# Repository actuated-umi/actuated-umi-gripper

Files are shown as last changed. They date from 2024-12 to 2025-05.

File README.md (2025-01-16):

# actuated-umi-gripper

<!-- PROJECT LOGO -->
<br />
<div align="center">
  <a href="https://github.com/actuated-umi/actuated-umi-gripper">
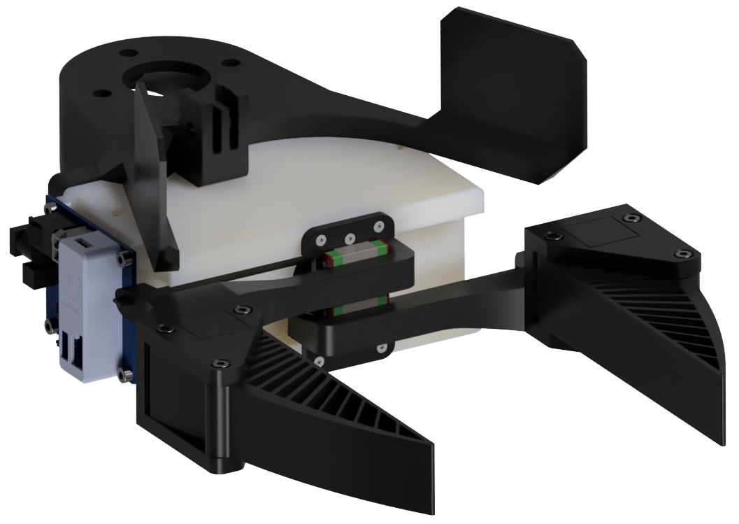
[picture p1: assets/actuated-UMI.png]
actuated-umi-gripper
    
  </a>

  <h3 align="center">Actuated UMI Gripper</h3>
  <h5 align="center">Erik Helmut*, Niklas Funk*, Tim Schneider, Jan Peters<br><em>*Equal contribution</em></h5>

  <p align="center">
    This repository provides an actuated, open-source version of the popular <a href="https://umi-gripper.github.io">UMI gripper</a>. 
    Designed to be cost-effective and modular, this gripper uses 3D-printed components to ensure accessibility and reproducibility. 
    With a Dynamixel motor for actuation, you can assemble the gripper yourself using the included design files and guidelines. 
    This repository contains the mechanical design files and printable components, enabling you to build and customize the gripper to suit your needs.
    This project would not have been possible without the earlier efforts of Chi et al. (2024) and the work of Clayton Haight. For more information about the prior works, please see the <a href="#acknowledgements">Acknowledgements</a> Section. <br />
    <a href="https://actuated-umi.github.io"><strong>For more information about actuated-UMI, visit the project page »</strong></a> <br />
  </p>
</div>

```
@inproceedings{helmut2024actuatedumi,
  author = {Helmut, Erik and Funk, Niklas and Schneider, Tim and Peters, Jan},
  title = {Actuated Version of the Universal Manipulation Interface Gripper},
  year = {2024},
  url  = {https://actuated-umi.github.io/}
}
```

<!-- TABLE OF CONTENTS -->
<details>
  <summary>Table of Contents</summary>
  <ol>
    <li>
      <a href="#bill-of-materials-bom">Bill of Materials (BoM)</a>
    </li>
    <li>
      <a href="#3d-printing-details">3D Printing Details</a>
    </li>
    <li>
      <a href="#assembly-guide">Assembly Guide</a>
    </li>
    <li>
      <a href="#usage">Usage</a>
    </li>
    <li>
      <a href="#acknowledgements">Acknowledgements</a>
    </li>
    <li>
      <a href="#license">License</a>
    </li>
    <li>
      <a href="#questions-and-contributing">Questions and Contributing</a>
    </li>
  </ol>
</details>

<!-- Bill of Materials -->
## Bill of Materials (BoM)
To build the actuated UMI gripper, you will need the following components. The list includes all necessary parts, along with links to purchase them online.

| Item | Quantity | Link |
|---|---|---|
| DYNAMIXEL XL430-W250-T | 1 | [MyBotShop](https://www.mybotshop.de/DYNAMIXEL-XL430-W250-T) |
| ROBOTIS DYNAMIXEL U2D2 | 1 | [MyBotShop](https://www.mybotshop.de/ROBOTIS-DYNAMIXEL-U2D2) |
| ROBOTIS DYNAMIXEL U2D2 POWER HUB | 1 | [MyBotShop](https://www.mybotshop.de/ROBOTIS-DYNAMIXEL-U2D2-Power-Hub) |
| Constant Force Spring (0.1x8x110) | 2 | [AliExpress](https://de.aliexpress.com/item/1005002310168061.html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) |
| Linear Rail & Carriage (80mm - MGN7C) | 2 | [AliExpress](https://de.aliexpress.com/item/1005004432783865.html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) |
| Flat Belt (width 5mm, thickness 1mm, length 300mm) | 1 | [KeilriemenExpress](https://www.keilriemenexpress.de/weitere-produkte/flachriemen-t150/neoprene-29306.html) |
| Heat Sets | 1 | [Amazon](https://www.amazon.de/Gewindeeinsatz-Einpressmutter-Gewindebuchsen-Kunststoff-Box-Kunststoffteiledurch/dp/B09B7F2XM3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) |
| Cylindrical Head Screws & Nuts (M3) | 1 | [Amazon](https://www.amazon.de/Sechskopf-Knopf-Zylinderschrauben-Gewindeschrauben-Sechskantschrauben-Maschinenschrauben/dp/B0B3MGZ7T2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ÅMÅŽÕÑ&crid=2AKHUVV2YXU0R&dib=eyJ2IjoiMSJ9.Gr0nOLkGHe8tC7VVlCThbb-3XEpHcX-eWT53-YGcYCqxmfHRqyxQLlBbVedU2xbw7nP-bcgj16am2vRgFkklYlSRtz3UCmgdAbns-Q1GhsDcldaA-3Puam8GKie6pPorMDHJwOL2cOysa3R_sP7CG7DVoxLh-96c7eJ_UxtuZCTM8XhOxgb_WTXR_o_CSQl1SargHb3wQWcaPaLm3-gPLkItAvxHlmyiryJryzrxORqWLVMNvA3O3HU5WPSbSJvE5MbQQ0Ben3iprgAdZbD7leyK8TchqTifKjEYljH00C23uNk1ystsyp9U24Gqirlc7gRdRJsspQR60bryparifMY5C1GV1TeXAIPXu3wbRVCFtpicU6AtxQ9DqY7fKWFWpiEUZiY6qYQhPYT9wVg1EHDFCk71AVnBrrAe34FDk-DPz8iuSDiNOT6HQFQlxaEw.pLT4ZCgQSOE5yQdMa6NFprSqQCqqWs3QW83IuaejpdI&dib_tag=se&keywords=m3x40&nsdOptOutParam=true&qid=1734961433&sprefix=m3x40%2Caps%2C150&sr=8-6&th=1) |
| Flat Head Screws (M2) | 1 | [Amazon](https://www.amazon.de/Innensechskantschrauben-Unterlegscheiben-Senkkopfschraube-Maschinenschrauben-Zylinderschrauben/dp/B0C6ZC3LB8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) |

<!-- 3D Printing Details -->
## 3D Printing Details
The gripper consists of several 3D-printed components that you can print yourself using a common FDM 3D printer with a standard nozzle diameter of 0.4 mm. We provide the design files for each component in the [`3d-printables`](3d-printables/) folder. The components are designed to be printed with PLA or similar materials. For all parts, we suggest using the infill pattern "Cubic" and adhesion method "Brim" to ensure optimal print quality and stability. We recommend the following settings for each 3D-printed component:

| Part Name | Layer Height | Wall Thickness | Top/Bottom Thickness | Infill | Support | Quantity |
|---|---|---|---|---|---|---|
| [Gripper Carriage Mount](3d-printables/actuated-UMI-gripper-carriage-mount.stl) | 0.2 mm | 1.2 mm | 1.2 mm | 100% | No | 1 |
| [Gripper Structure](3d-printables/actuated-UMI-gripper-structure.stl) | 0.2 mm | 2.4 mm | 1.2 mm | 40% | Yes | 1 |
| [Jaw Left](3d-printables/actuated-UMI-jaw-left.stl) | 0.2 mm | 2.4 mm | 1.2 mm | 40% | Yes | 1 |
| [Jaw Right](3d-printables/actuated-UMI-jaw-right.stl) | 0.2 mm | 2.4 mm | 1.2 mm | 40% | Yes | 1 |
| [CF Sprint Idler](3d-printables/OpenGrip-cf-spring-idler.stl) | 0.2 mm | 1.2 mm | 1.2 mm | 100% | No | 2
| [Gripper Drive Pulley](3d-printables/OpenGrip-gripper-drive-pulley.stl) | 0.2 mm | 1.2 mm | 1.2 mm | 100% | Yes | 1
| [Gripper Fingers](3d-printables/UMI-gripper-soft-gripper-finger.stl) | 0.2 mm | 1.2 mm | 1.2 mm | 40% | No | 2 |
| [Franka Gripper Mount](3d-printables/UMI-wsg50-franka-mount-gripper-mount.stl) | 0.2 mm | 1.2 mm | 1.2 mm | 40% | No | 1 |

Note: If you want to print the fingers with TPU, please follow the setting from the [UMI Gripper](https://umi-gripper.github.io) hardware guide.

<!-- Assembly Guide -->
## Assembly Guide
We provide a comprehensive, step-by-step assembly guide to help you build the gripper with ease. The video tutorial walks you through each step, ensuring a clear and straightforward assembly experience. You can find the video tutorial below:

<a href="https://www.youtube.com/watch?v=XodgLZ3qirM">
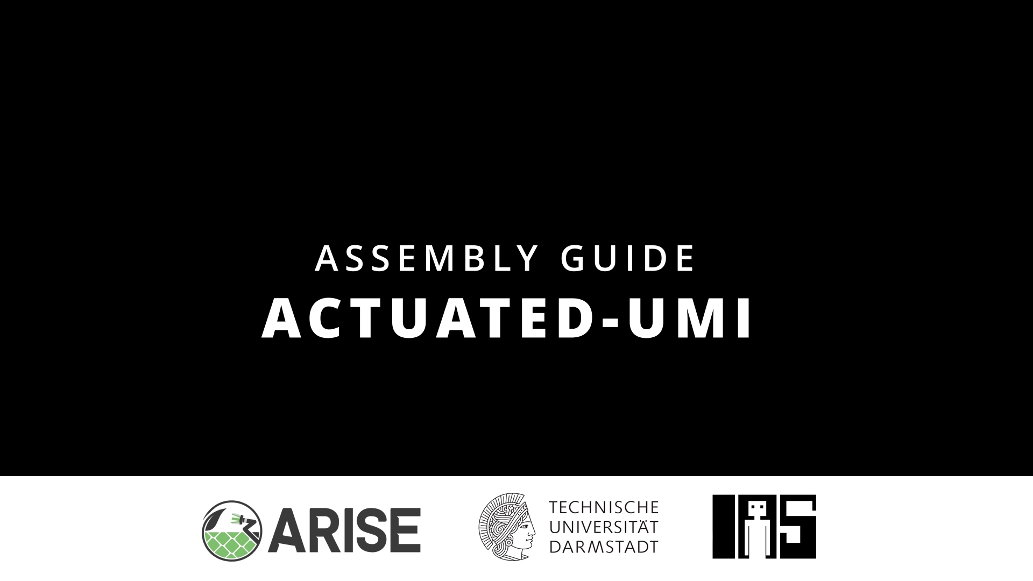
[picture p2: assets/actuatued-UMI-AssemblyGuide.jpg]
Assembly Guide ACTUATED-UMI
    
  </a>

<!-- Usage -->
## Usage
To use the gripper after it is fully assembled, you will need the appropriate software to control it. We recommend using the [Dynamixel API](https://github.com/TimSchneider42/dynamixel-api) developed by our team. This API provides a comprehensive set of tools and functions to interface with Dynamixel motors, which are used in the actuated UMI gripper.

The repository includes detailed instructions on how to install and use the API, as well as example code to get you started. By following the guidelines provided in the Dynamixel API repository, you can easily integrate the gripper into your projects and control its movements programmatically.

<!-- Acknowledgements -->
## Acknowledgements
This work heavily builds upon the following prior efforts. It would not have been possible without them.

- C. Chi, Z. Xu, C. Pan, E. Cousineau, B. Burchfiel, S. Feng, R. Tedrake, and S. Song, "Universal Manipulation Interface: In-The-Wild Robot Teaching Without In-The-Wild Robots," in Proc. Robotics: Science and Systems (RSS), 2024. We used the [UMI Gripper](https://umi-gripper.github.io) as a key reference for our design, aiming to closely replicate its functionality and form. 
- Clayton Haight, creator of [OpenGrip](https://github.com/clayhaight01/OpenGrip). The OpenGrip gripper mechanism served as the initial design starting point for our own gripper development.
- Stan Markwell, for providing CAD files of the ROBOTIS U2D2 Power Hub Board & U2D2, available on [GrabCAD](https://grabcad.com/library/robotis_u2d2_power_hub_board-1).

<!-- License -->
## License
This project is licensed under the MIT License. However, it incorporates third-party content, which retains its original license terms. Details are as follows:

- **Third-Party Content**: Portions of this project include content from [UMI Gripper](https://umi-gripper.github.io) licensed under the MIT License. The original license file for these materials can be found in [LICENSE_THIRD_PARTY](LICENSE_THIRD_PARTY).

- **Your Contributions**: All other content in this project, created by [Actuated-UMI](https://actuated-umi.github.io), is licensed under the MIT License. You can find the license file for this project in [LICENSE](LICENSE).

For clarity:
- You are free to use, modify, and distribute this project under the terms of the MIT License.
- Please ensure compliance with the license terms for the included third-party content.

<!-- Questions and Contributing -->
## Questions and Contributing
If you have any questions or need help with building the gripper, please create an <a href="https://github.com/actuated-umi/actuated-umi-gripper/issues/new/">issue</a>.

We also welcome contributions to this repository, including new 3D models or other improvements. If you would like to contribute, please <a href="https://github.com/actuated-umi/actuated-umi-gripper/fork">fork</a> this repository and submit a <a href="https://github.com/actuated-umi/actuated-umi-gripper/compare">pull request</a> with your changes, or reach out to erik.helmut1 [at] gmail [dot] de.

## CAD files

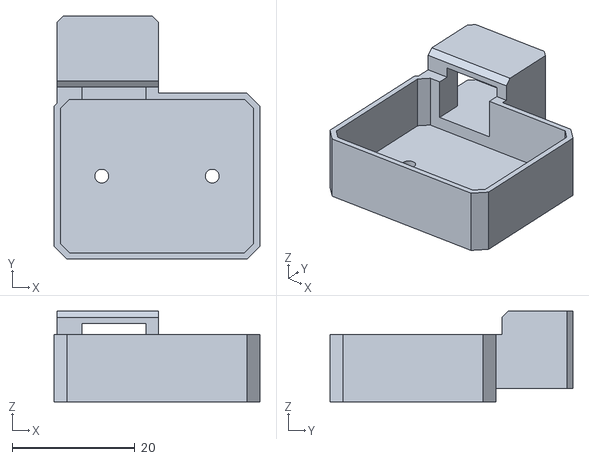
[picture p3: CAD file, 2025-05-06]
3d-printables/actuated-UMI-v2/gelsight-mini-integrated-cable-protection-mirrored.stl
33.5 x 39.6 x 14.8

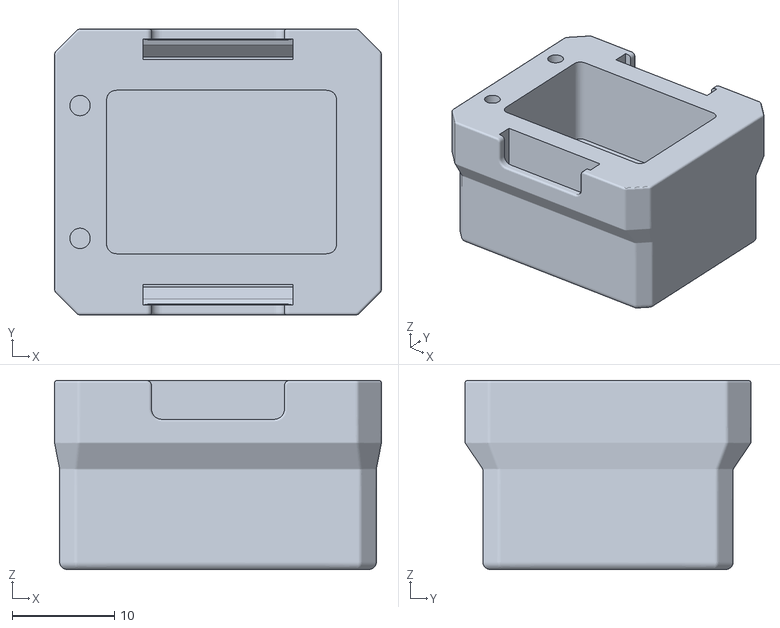
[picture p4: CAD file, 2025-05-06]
3d-printables/actuated-UMI-v2/gelsight-mini-shell-placeholder.stl
32.0 x 28.0 x 18.5

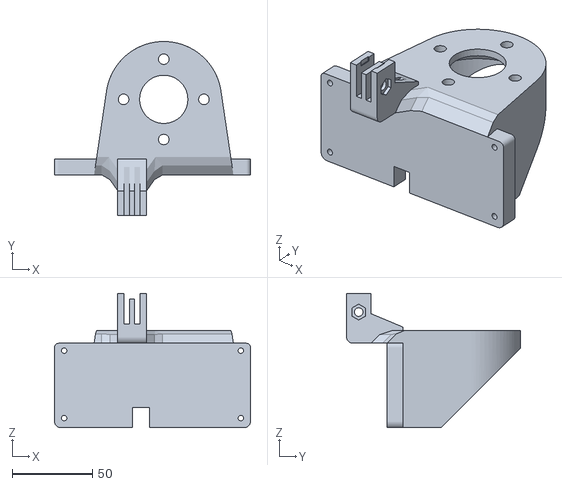
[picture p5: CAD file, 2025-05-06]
3d-printables/actuated-UMI-v2/actuated-UMI-franka-gripper-mount.stl
122.0 x 108.3 x 83.7

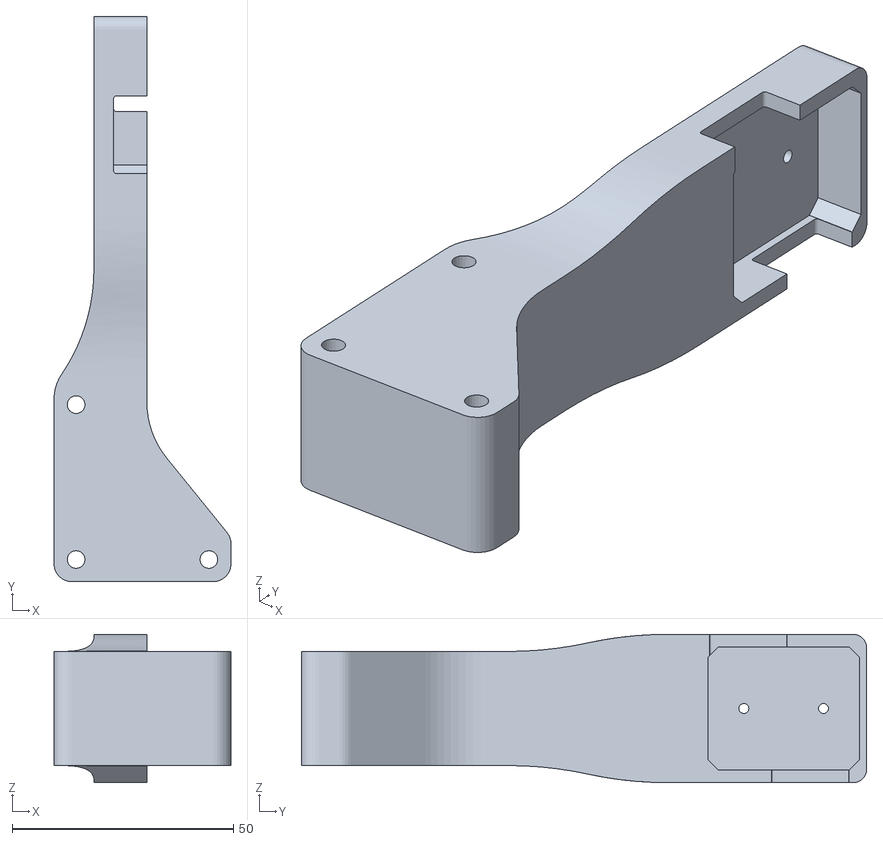
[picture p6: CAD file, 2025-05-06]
3d-printables/actuated-UMI-v2/gelsight-mini-finger-cable-protection.stl
40.0 x 127.8 x 33.5

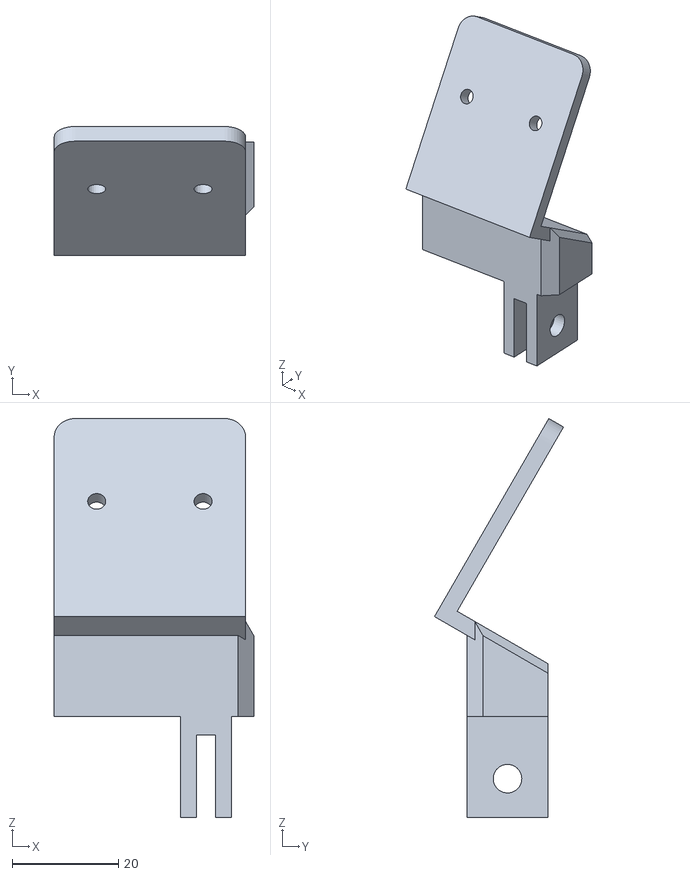
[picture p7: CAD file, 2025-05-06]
3d-printables/actuated-UMI-v2/camera-mount-D405.stl
37.6 x 24.3 x 75.0

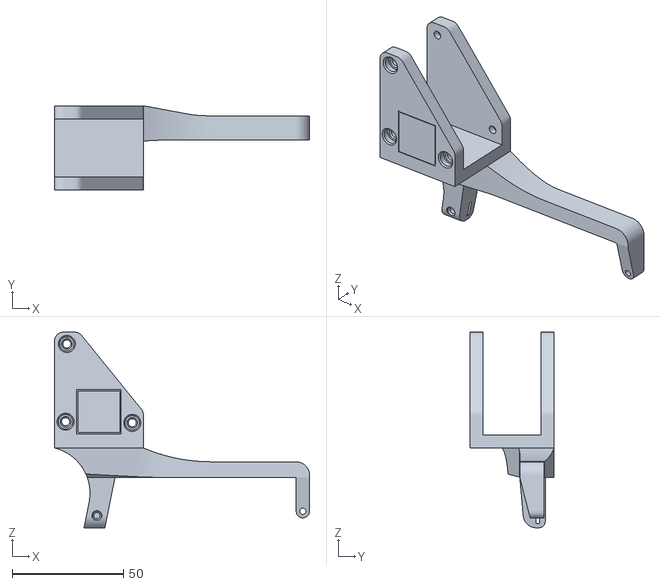
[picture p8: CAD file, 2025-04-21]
3d-printables/actuated-UMI-v2/actuated-UMI-jaw-left.stl
114.8 x 38.0 x 88.1

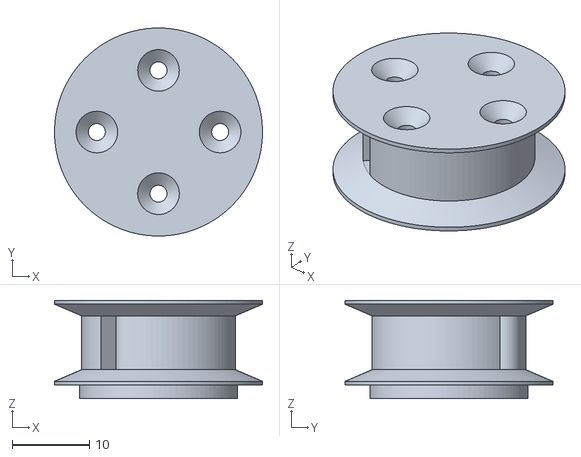
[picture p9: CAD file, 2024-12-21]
3d-printables/actuated-UMI-v2/OpenGrip-gripper-drive-pulley.stl
27.0 x 27.0 x 12.8

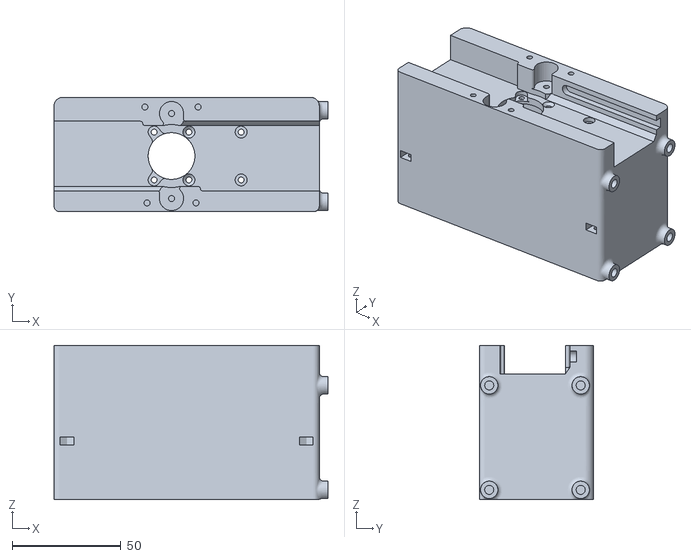
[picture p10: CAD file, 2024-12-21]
3d-printables/actuated-UMI-v2/actuated-UMI-gripper-structure.stl
126.0 x 52.6 x 70.9

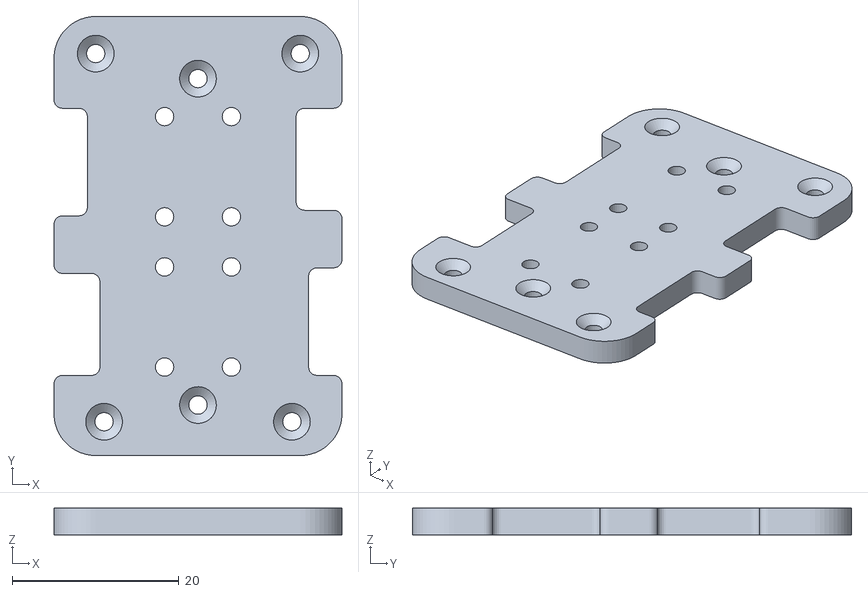
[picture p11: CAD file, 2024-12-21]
3d-printables/actuated-UMI-v2/actuated-UMI-gripper-carriage-mount.stl
34.5 x 52.6 x 3.17

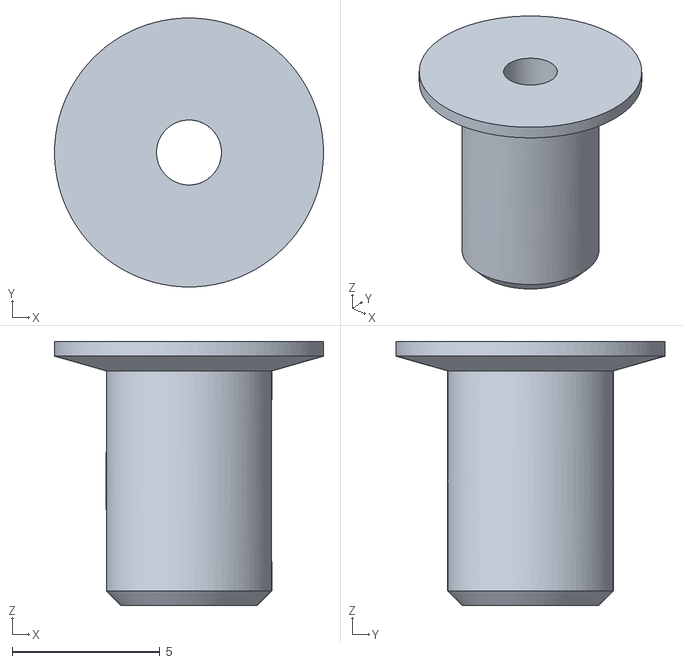
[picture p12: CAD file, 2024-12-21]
3d-printables/actuated-UMI-v2/OpenGrip-cf-spring-idler.stl
9.10 x 9.10 x 8.94

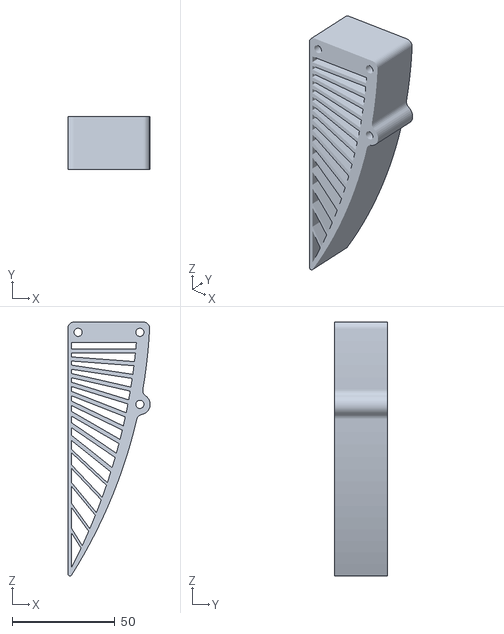
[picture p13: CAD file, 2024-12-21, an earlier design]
3d-printables/actuated-UMI-v1/UMI-gripper-soft-gripper-finger.stl
40.0 x 25.8 x 123.4

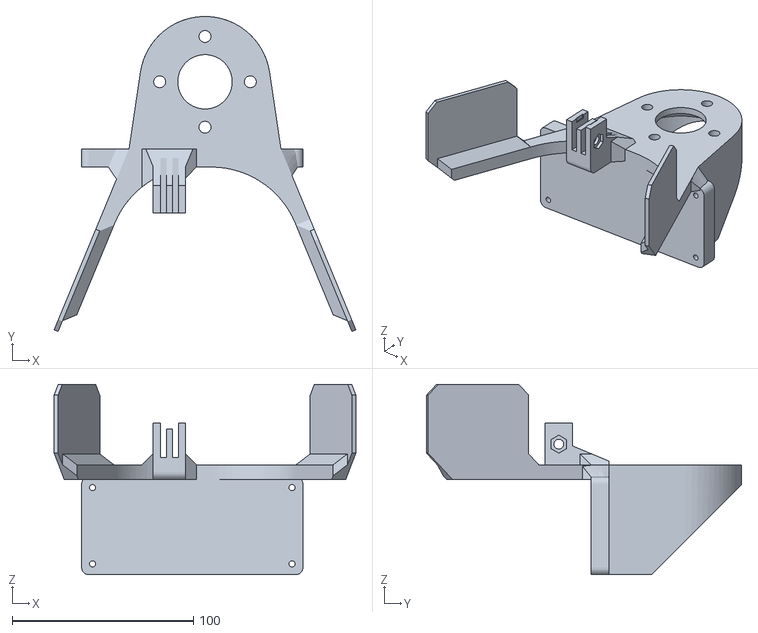
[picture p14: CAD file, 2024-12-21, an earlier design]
3d-printables/actuated-UMI-v1/UMI-wsg50-franka-mount-gripper-mount.stl
166.4 x 173.6 x 105.0

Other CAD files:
3d-printables/actuated-UMI-v2/gelsight-mini-integrated-cable-protection.stl
3d-printables/actuated-UMI-v2/actuated-UMI-jaw-right.stl
3d-printables/actuated-UMI-v1/actuated-UMI-jaw-right.stl

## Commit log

2024-12-21 add actuated-umi assembly
2024-12-21 add 3d-printables
    [OpenGrip-cf-spring-idler.stl, OpenGrip-gripper-drive-pulley.stl, UMI-gripper-soft-gripper-finger.stl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]
2025-01-13 update assembly guide thumbnail
2025-04-21 make hole for heat sets smaller
    [actuated-UMI-jaw-left.stl, actuated-UMI-jaw-right.stl]
2025-05-06 add v2 version of gripper
    [OpenGrip-cf-spring-idler.stl, OpenGrip-gripper-drive-pulley.stl, UMI-gripper-soft-gripper-finger.stl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]
